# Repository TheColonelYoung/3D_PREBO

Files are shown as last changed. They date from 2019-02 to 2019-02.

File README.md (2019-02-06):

# **3D_PrEBo**
<br />

This project is 3D printer expansion board.  Add more fan controllers, TMC2130 wiring support, induction probe voltage convertor, LED lighting (supports WS1812).

This board was designed for best compatibility with MKS GEN L, but is compatible for example with BIGTREETECH SKR 1.1.

### **Board features**

- Stepdown regulator - from up to 35V to 12V
    - can by bypassed by jumper, if you have 12V power supply by solder jumper
    - minimal volatage for regulator is 15V
    - based on L5973D (up to 2A)

- Advanced fan controll
    - you can controll up to 8 fans
    - 1 fan is 4 pin, others are 3 pin with additional transistor
    - speed input for fan is from motherboard (EXP_X connectors)
    - one of fans can be used as regulated fan for hotend cooling (temperature dependent cooling)
    - Fan voltage can be selected from , Vin, 12V, 5V via solder bridges
    - Expected fan distibution: 1x Motherboard fan, 2x part cooling fans, 1x hotend cooling fan, 4 fans for other usage (maybe motors)
    - input signal for fans can be chain, one signal can drive more fans

- Probe connector
    - serve as input from inductive probe
    - Voltage divider, designed as 24V -> 5V

- TMC2130 wiring
    - helps to keep wiring simple and clean
    - holes in board for simple wiring and better airflow around cables
    - 4 pin connectors
    - if motherboard didn't have enough pins, in Marlin 2.0, can be TMC2130 enabled via SPI, so EN pin for driver can be used as Chip select fro SPI
    
- LED light
    - means as print part lighting
    - selectable voltage (5V or 12 V) by solder jumper

- 5 in one connector
    - Onboard RJ-45 connectors and UTP cable (8-wires)
    - As HUB is used second board mounted on printer head
    - Fans, Led outputs and both outputs (6in1 and separe)
    - Pins:
        - 1x GND, 1x 12V,
        - 3x FAN
        - 1x X Endstop (or 5V Z probe if on hat isn't X endstop)
        - 2x LED lights

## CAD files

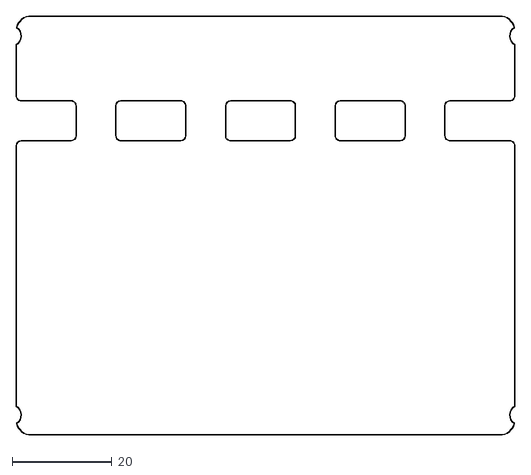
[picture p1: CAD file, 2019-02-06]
Expansion_board/3D_PReBo_outlines.dxf
100.0 x 84.0

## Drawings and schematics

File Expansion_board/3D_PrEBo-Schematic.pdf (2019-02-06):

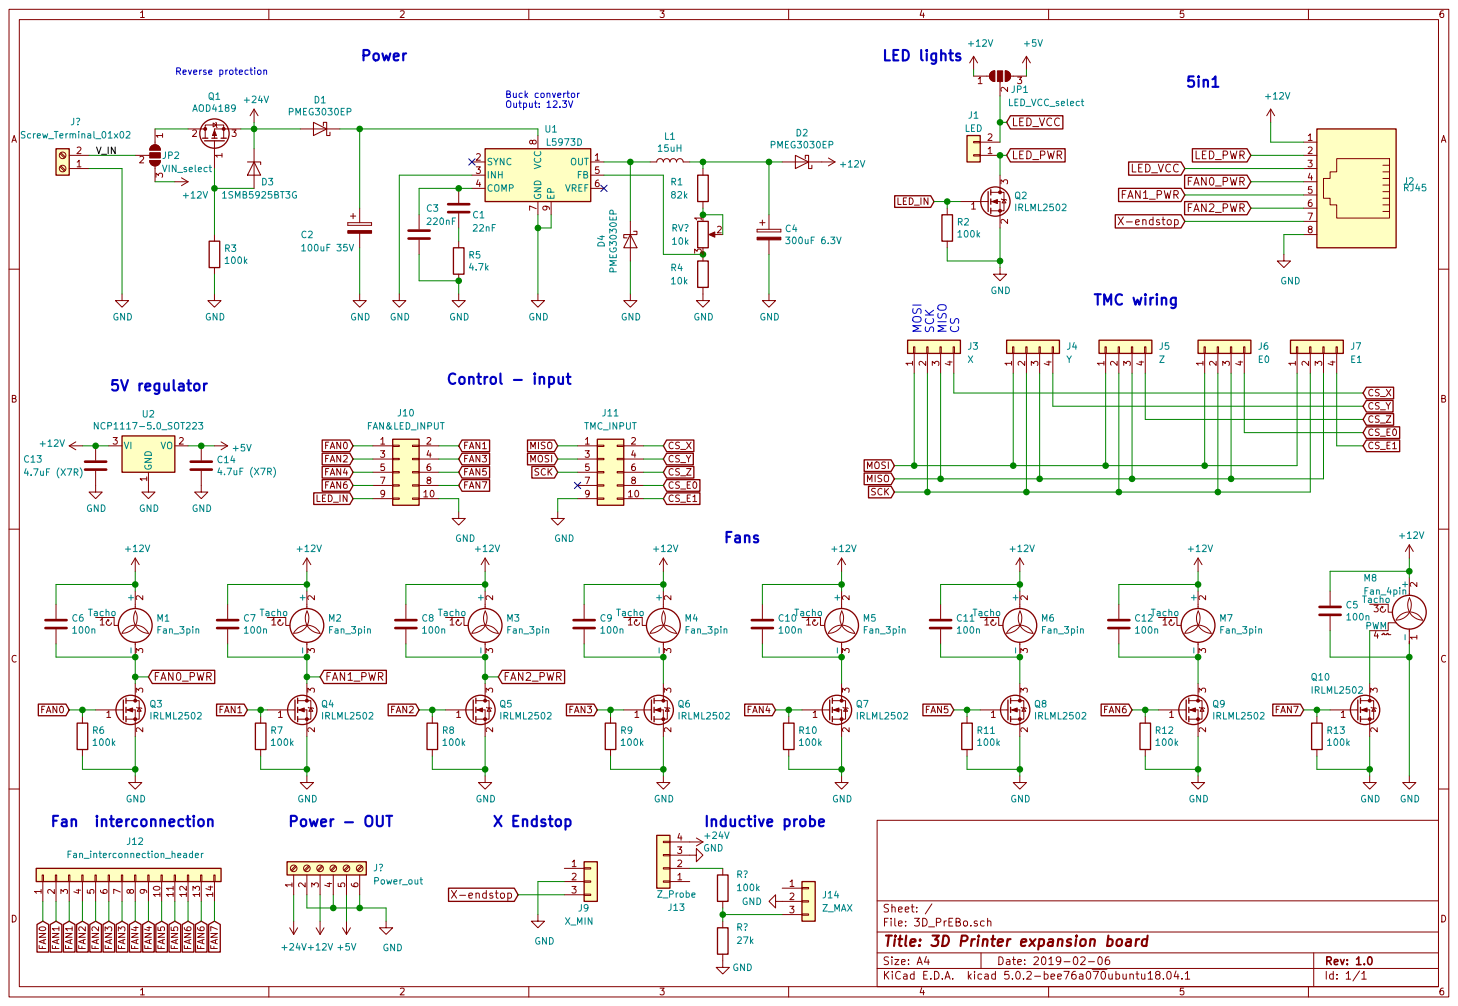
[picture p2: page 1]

File: 3D_PrEBo.sch Sheet: /
Id: 1/1 Title: 3D Printer expansion board

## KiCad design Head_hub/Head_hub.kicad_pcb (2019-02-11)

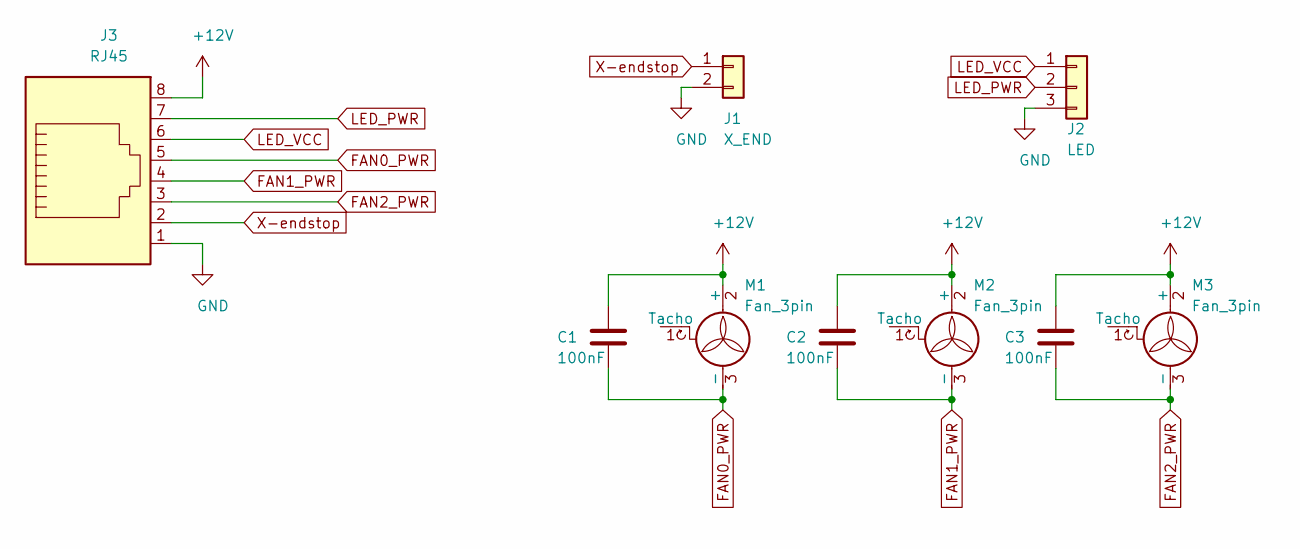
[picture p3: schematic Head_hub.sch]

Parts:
C1, C2, C3: 100nF; C_0603_1608Metric
J1: X_END; JST_XH_B02B-XH-A_1x02_P2.50mm_Vertical
J2: LED; JST_XH_B03B-XH-A_1x03_P2.50mm_Vertical
J3: RJ45; RJ45_Amphenol_54602-x08_Horizontal
M1, M2, M3: Fan_3pin; FanPinHeader_1x03_P2.54mm_Vertical

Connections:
+12V: C1.1, C2.1, C3.1, J3.8, M1.2 (+), M2.2 (+), M3.2 (+)
FAN0_PWR: C1.2, J3.5, M1.3 (-)
FAN1_PWR: C2.2, J3.4, M2.3 (-)
FAN2_PWR: C3.2, J3.3, M3.3 (-)
GND: J1.2, J2.3, J3.1
LED_PWR: J2.2, J3.7
LED_VCC: J2.1, J3.6
X-endstop: J1.1, J3.2

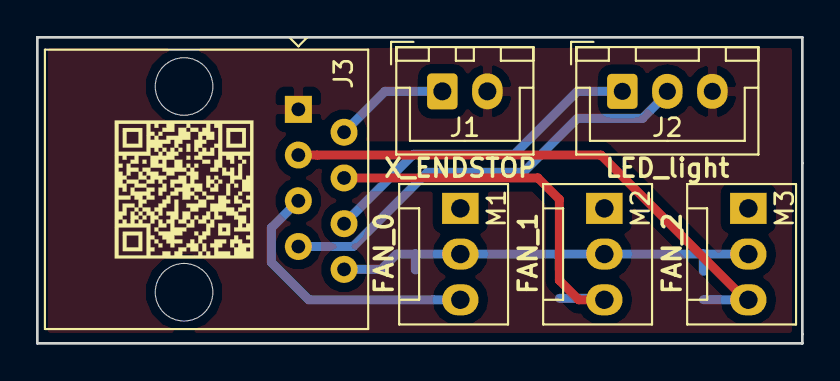
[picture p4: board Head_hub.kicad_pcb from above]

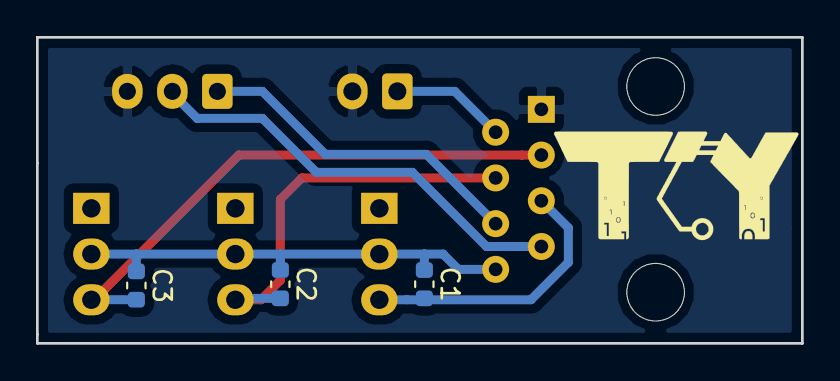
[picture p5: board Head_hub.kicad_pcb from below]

Board: 2 copper layers, 42.5 x 17.0 mm, 9 parts (3 on the bottom side), 8 nets.

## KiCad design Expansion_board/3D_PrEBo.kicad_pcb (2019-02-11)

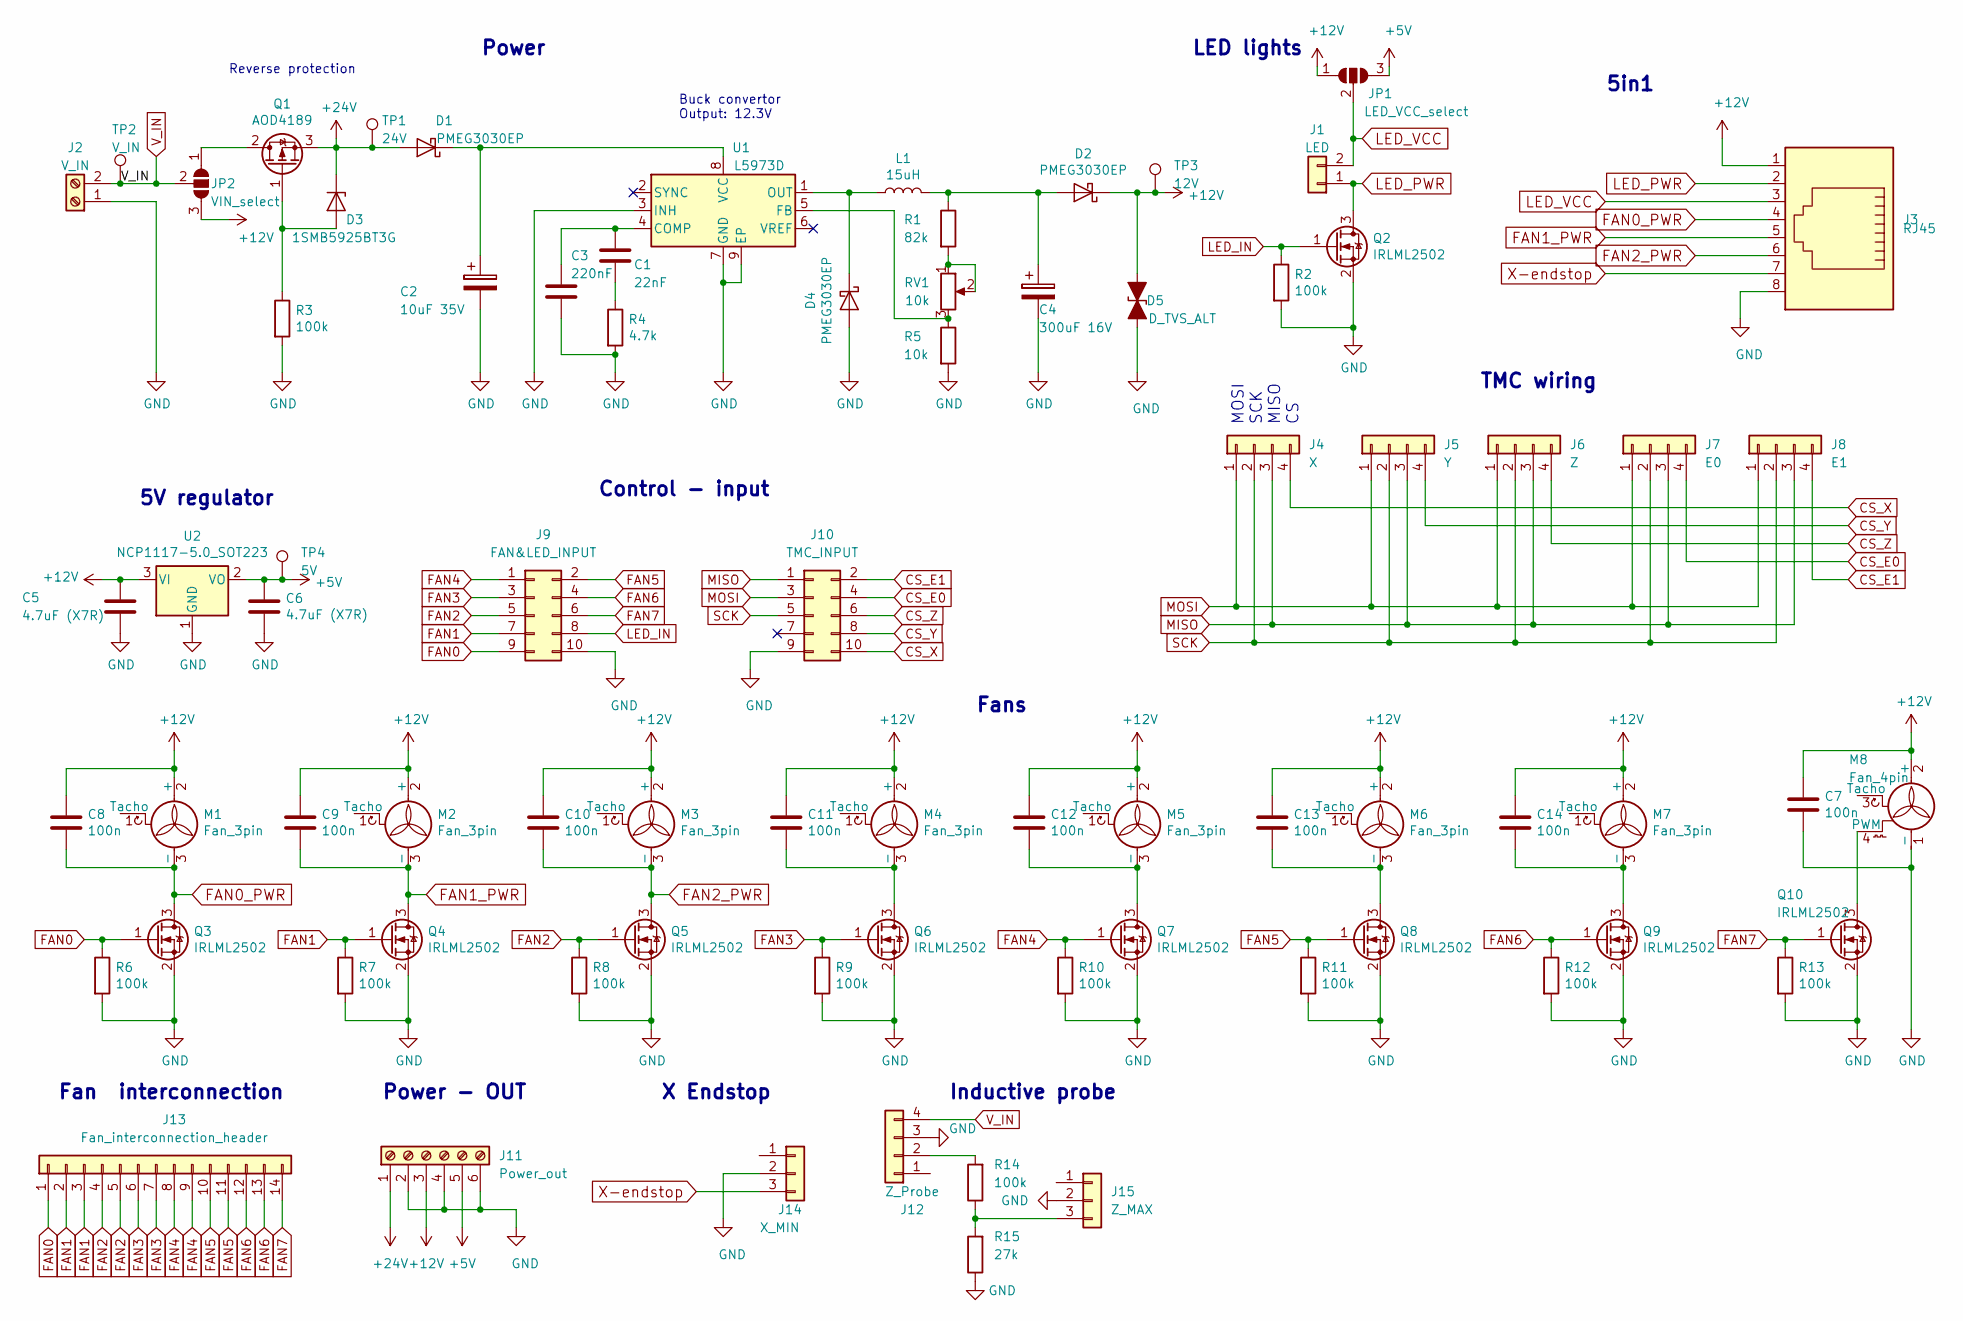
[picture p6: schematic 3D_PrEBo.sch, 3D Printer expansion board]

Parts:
C1: 22nF; C_0603_1608Metric
C2: 10uF 35V; C_2816_7142Metric_Pad3.20x4.45mm_HandSolder
C3: 220nF; C_0603_1608Metric
C4: 300uF 16V; CP_Elec_8x10.5
C5, C6: 4.7uF (X7R); C_0805_2012Metric
C7, C8, C9, C10, C11, C12, C13, C14: 100n; C_0603_1608Metric
D1, D2, D4: PMEG3030EP; D_SMB
D3: 1SMB5925BT3G; D_SMB
D5: D_TVS_ALT; D_SMA
J1: LED; JST_XH_B02B-XH-A_1x02_P2.50mm_Vertical
J2: V_IN; TerminalBlock_Phoenix_MKDS-1,5-2_1x02_P5.00mm_Horizontal
J3: RJ45; RJ45_Amphenol_54602-x08_Horizontal
J4: X; PinHeader_1x04_P2.54mm_Horizontal
J5: Y; PinHeader_1x04_P2.54mm_Horizontal
J6: Z; PinHeader_1x04_P2.54mm_Horizontal
J7: E0; PinHeader_1x04_P2.54mm_Horizontal
J8: E1; PinHeader_1x04_P2.54mm_Horizontal
J9: FAN&LED_INPUT; IDC-Header_2x05_P2.54mm_Horizontal
J10: TMC_INPUT; IDC-Header_2x05_P2.54mm_Horizontal
J11: Power_out; TerminalBlock_Phoenix_MKDS-1,5-6_1x06_P5.00mm_Horizontal
J12: Z_Probe; JST_XH_B04B-XH-A_1x04_P2.50mm_Vertical
J13: Fan_interconnection_header; PinHeader_1x14_P2.54mm_Vertical
J14: X_MIN; JST_XH_S03B-XH-A-1_1x03_P2.50mm_Horizontal
J15: Z_MAX; JST_XH_S03B-XH-A-1_1x03_P2.50mm_Horizontal
JP1: LED_VCC_select; SolderJumper-3_P1.3mm_Open_RoundedPad1.0x1.5mm
JP2: VIN_select; SolderJumper-3_P1.3mm_Open_RoundedPad1.0x1.5mm
L1: 15uH; L_Neosid_Ms85
M1, M2, M3, M4, M5, M6, M7: Fan_3pin; JST_XH_S03B-XH-A_1x03_P2.50mm_Horizontal
M8: Fan_4pin; JST_XH_S04B-XH-A_1x04_P2.50mm_Horizontal
Q1: AOD4189; TO-252-2
Q2, Q3, Q4, Q5, Q6, Q7, Q8, Q9, Q10: IRLML2502; TSOT-23
R1: 82k; R_0603_1608Metric
R2, R3, R6, R7, R8, R9, R10, R11, R12, R13, R14: 100k; R_0603_1608Metric
R4: 4.7k; R_0603_1608Metric
R5: 10k; R_0603_1608Metric
R15: 27k; R_0603_1608Metric
RV1: 10k; Potentiometer_Bourns_3214J_Horizontal
TP1: 24V; TestPoint_THTPad_D1.5mm_Drill0.7mm
TP2: V_IN; TestPoint_THTPad_D1.5mm_Drill0.7mm
TP3: 12V; TestPoint_THTPad_D1.5mm_Drill0.7mm
TP4: 5V; TestPoint_THTPad_D1.5mm_Drill0.7mm
U1: L5973D; HTSOP-8-1EP_3.9x4.9mm_P1.27mm_EP2.4x3.2mm
U2: NCP1117-5.0_SOT223; SOT-223-3_TabPin2

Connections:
+5V: C6.1, J11.5, JP1.3 (B), TP4.1, U2.2 (VO)
+12V: C5.1, C7.1, C8.1, C9.1, C10.1, C11.1, C12.1, C13.1, C14.1, D2.1 (K), D5.2 (A2), J3.1, J11.3, JP1.1 (A), JP2.3 (B), M1.2 (+), M2.2 (+), M3.2 (+), M4.2 (+), M5.2 (+), M6.2 (+), M7.2 (+), M8.2 (+), TP3.1, U2.3 (VI)
+24V: D1.2 (A), D3.1 (K), J11.1, Q1.3 (S), TP1.1
CS_E0: J7.4, J10.4
CS_E1: J8.4, J10.2
CS_X: J4.4, J10.10
CS_Y: J5.4, J10.8
CS_Z: J6.4, J10.6
FAN0: J9.9, J13.1, Q3.1 (G), R6.1
FAN0_PWR: C8.2, J3.4, M1.3 (-), Q3.3 (D)
FAN1: J9.7, J13.2, J13.3, Q4.1 (G), R7.1
FAN1_PWR: C9.2, J3.5, M2.3 (-), Q4.3 (D)
FAN2: J9.5, J13.4, J13.5, Q5.1 (G), R8.1
FAN2_PWR: C10.2, J3.6, M3.3 (-), Q5.3 (D)
FAN3: J9.3, J13.6, J13.7, Q6.1 (G), R9.1
FAN4: J9.1, J13.8, J13.9, Q7.1 (G), R10.1
FAN5: J9.2, J13.10, J13.11, Q8.1 (G), R11.1
FAN6: J9.4, J13.12, J13.13, Q9.1 (G), R12.1
FAN7: J9.6, J13.14, Q10.1 (G), R13.1
GND: C2.2, C3.2, C4.2, C5.2, C6.2, C7.2, D4.2 (A), D5.1 (A1), J2.1, J3.8, J9.10, J10.9, J11.2, J11.4, J11.6, J12.3, J14.2, J15.2, M8.1 (-), Q2.2 (S), Q3.2 (S), Q4.2 (S), Q5.2 (S), Q6.2 (S), Q7.2 (S), Q8.2 (S), Q9.2 (S), Q10.2 (S), R2.2, R3.2, R4.2, R5.2, R6.2, R7.2, R8.2, R9.2, R10.2, R11.2, R12.2, R13.2, R15.1, U1.3 (INH), U1.7 (GND), U1.9 (EP), U2.1 (GND)
LED_IN: J9.8, Q2.1 (G), R2.1
LED_PWR: J1.1, J3.2, Q2.3 (D)
LED_VCC: J1.2, J3.3, JP1.2 (C)
MISO: J4.3, J5.3, J6.3, J7.3, J8.3, J10.1
MOSI: J4.1, J5.1, J6.1, J7.1, J8.1, J10.3
unnamed: C1.1, C3.1, U1.4 (COMP)
unnamed: C1.2, R4.1
unnamed: C2.1, D1.1 (K), U1.8 (VCC)
unnamed: C4.1, D2.2 (A), L1.2, R1.1
unnamed: C11.2, M4.3 (-), Q6.3 (D)
unnamed: C12.2, M5.3 (-), Q7.3 (D)
unnamed: C13.2, M6.3 (-), Q8.3 (D)
unnamed: C14.2, M7.3 (-), Q9.3 (D)
unnamed: D3.2 (A), Q1.1 (G), R3.1
unnamed: D4.1 (K), L1.1, U1.1 (OUT)
unnamed: J12.2, R14.2
unnamed: J15.3, R14.1, R15.2
unnamed: JP2.1 (A), Q1.2 (D)
unnamed: M8.4 (PWM), Q10.3 (D)
unnamed: R1.2, RV1.1, RV1.2
unnamed: R5.1, RV1.3, U1.5 (FB)
SCK: J4.2, J5.2, J6.2, J7.2, J8.2, J10.5
V_IN: J2.2, J12.4, JP2.2 (C), TP2.1
X-endstop: J3.7, J14.3

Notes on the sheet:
Reverse protection
Buck convertor Output: 12.3V
5V regulator
Fan interconnection
Inductive probe
TMC wiring
MOSI SCK MISO CS
Fans
Power
5in1
LED lights
Power - OUT
X Endstop
Control - input

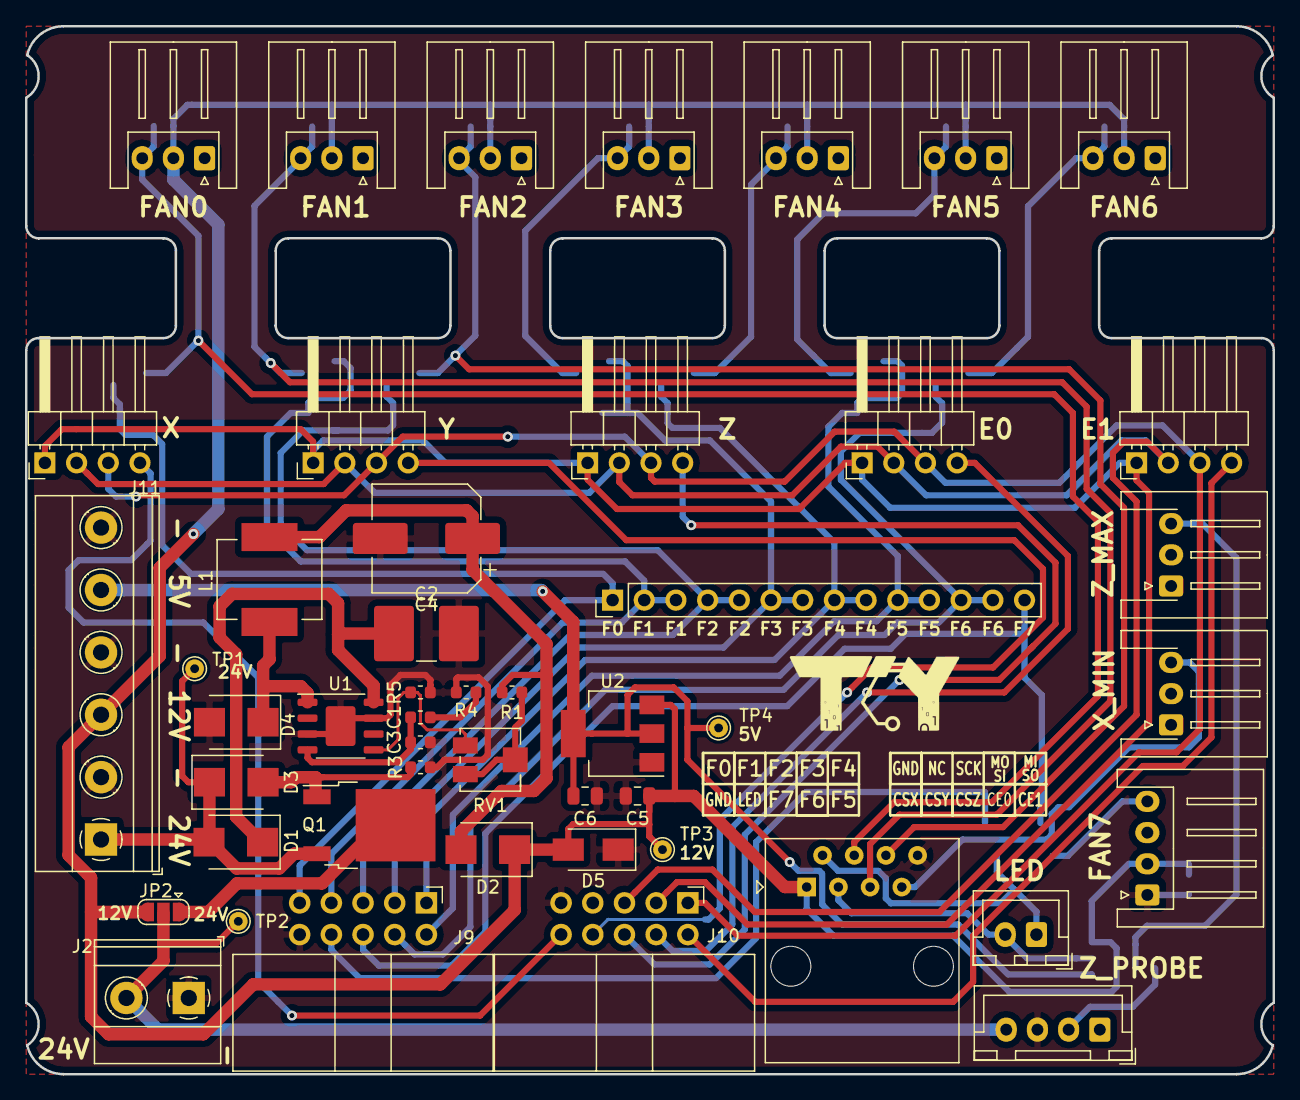
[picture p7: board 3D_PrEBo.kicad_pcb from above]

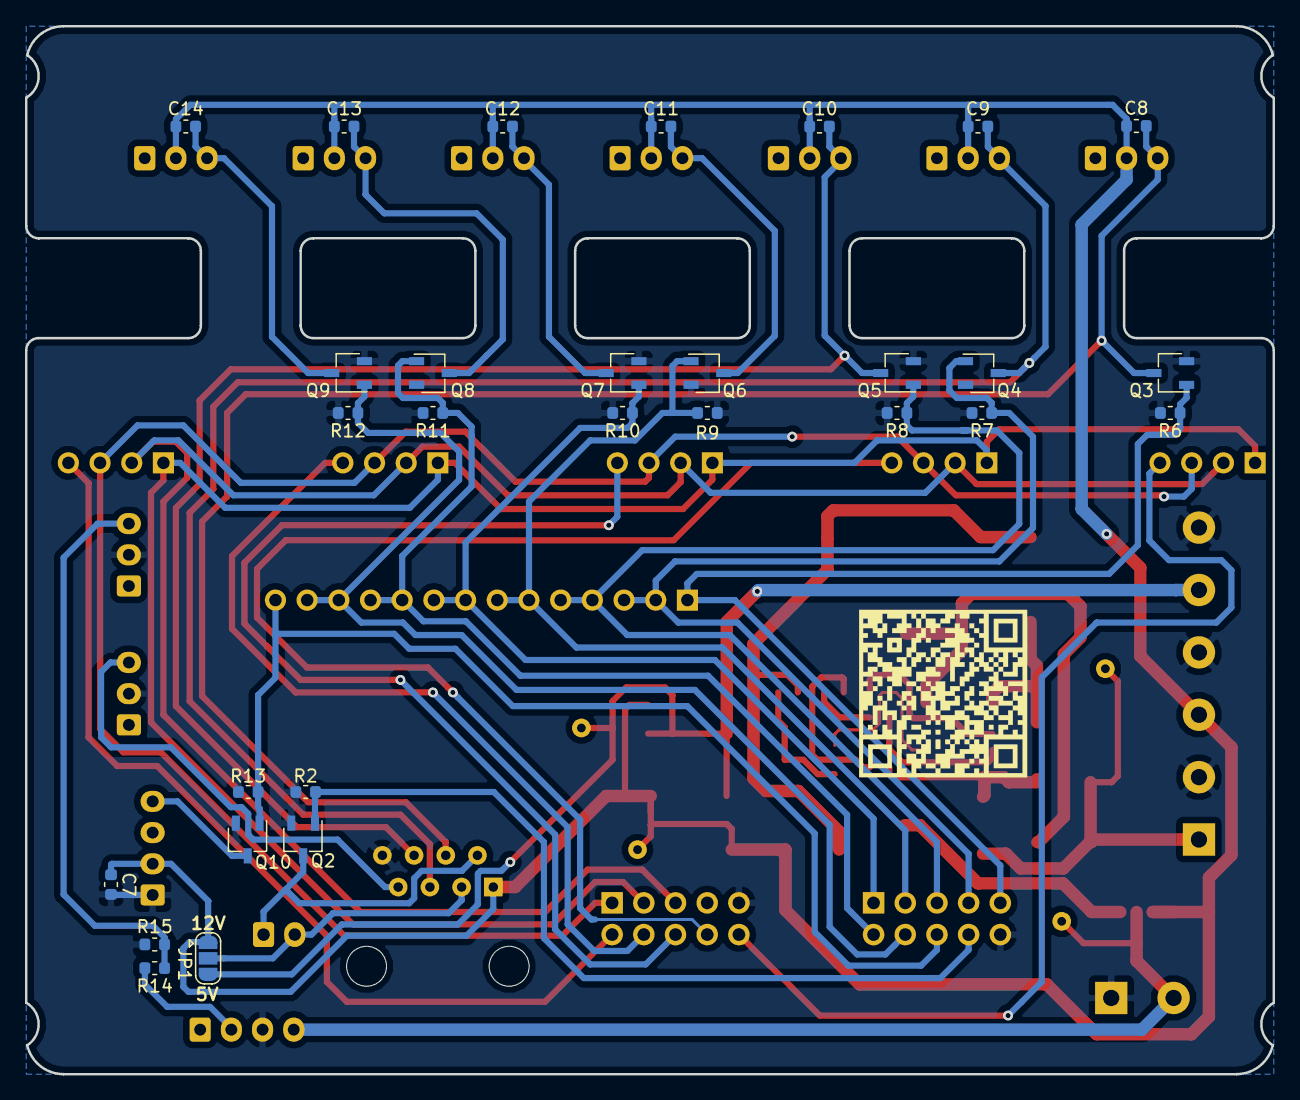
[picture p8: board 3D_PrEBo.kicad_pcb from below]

Board: 2 copper layers, 100.0 x 84.0 mm, 77 parts (29 on the bottom side), 44 nets.

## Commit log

2019-02-04 Add license, update specification in README.md
    Add board features: power management, fan controll, 6in1 connector, TMC2130.
2019-02-06 Schematic: Expansion board schematic, first draft
    TODO: inductive probe, Buck converter voltage settings
    [3D_PrEBo.kicad_pcb, 3D_PrEBo.sch]
2019-02-06 Schematic: Add inductive probe and set voltage of buck converter
    [3D_PrEBo.sch]
2019-02-06 Schematic: Add schematic in pdf, minor part shifting in schema
    [3D_PrEBo.kicad_pcb, 3D_PrEBo.sch]
2019-02-06 Schema: Head_HUB: Initial schema and package assign
    [Head_hub.kicad_pcb, Head_hub.sch]
2019-02-06 Schema: Update part labels, Rewrite project description
    [3D_PrEBo.sch]
2019-02-06 Head_HUB: PCB: Routing done
    [Head_hub.sch]
2019-02-06 Expansion_board: PCB: Add PCB outlines, position some parts on PCB
    [3D_PReBo_outlines.dxf, 3D_PrEBo.kicad_pcb, 3D_PrEBo.sch]
2019-02-07 Expansion_board: PCB: Place all parts, routing of voltage regulator
    Change horizontal fan connector to vertical.
    Pour cooper planes on both sides.
    [3D_PrEBo.kicad_pcb, 3D_PrEBo.sch]
2019-02-07 Expansiopn_board: PCB: Routing done, Silk screen in progress
    [3D_PrEBo.kicad_pcb, 3D_PrEBo.sch]
2019-02-08 Expansion_board: PCB: Rotate FAN transistors, update bottom silk screen
    [3D_PrEBo.kicad_pcb]
2019-02-08 Expansion_board: PCB: Fix some design limitations, move endstop connector
    [3D_PrEBo.kicad_pcb]
2019-02-10 Expansion_board: Schema: Change in buck convertor capacitors, add transil
    change capacitors to correct packages and voltages
    add transil to convertor output as overvoltage protection
    [3D_PrEBo.sch]
2019-02-10 Expansion_board: PCB: Add trnasil, reroute capacitors
    [3D_PrEBo.kicad_pcb, 3D_PrEBo.sch]
2019-02-11 Expansion_board: PCB: Update logo position
    [3D_PrEBo.kicad_pcb]
2019-02-11 Expansion_board: PCB: Updated silkscreen for power connectors
    [3D_PrEBo.kicad_pcb]
2019-02-11 Expansion_board: Add test points for voltages
    [3D_PrEBo.kicad_pcb, 3D_PrEBo.sch]
2019-02-11 Expansion_board: Generate gerber data for fabrication
    [3D_PrEBo-B.Cu.gbl, 3D_PrEBo-B.Mask.gbs, 3D_PrEBo-B.SilkS.gbo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]
2019-02-11 Expansion_board: PCB: Add QR code with link to GitHub repository
    [3D_PrEBo.kicad_pcb]
2019-02-11 Expansion_board: Gerber: Add .zip with gerber files, removed unnecessary non-ziped gerber files
    [3D_PrEBo-B.Cu.gbl, 3D_PrEBo-B.Mask.gbs, 3D_PrEBo-B.SilkS.gbo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]
2019-02-11 Head_HUB: PCB: Add QR code with link to GitHub repository
    [Head_hub.kicad_pcb]
2019-02-11 Head_HUB: Gerber: Add .zip with gerber files for fabrications

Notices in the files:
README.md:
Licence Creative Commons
